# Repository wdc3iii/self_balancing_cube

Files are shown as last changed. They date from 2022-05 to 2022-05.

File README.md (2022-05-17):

# Table of Contents

* TOC
{:toc}

# Introduction
This project tackles a classic linear controls problem: balancing an inherently unstable system, and making the system robust to physical disturbances.  Taking inspiration from the rather impressive [Cubli](https://robohub.org/swiss-robots-cubli-a-cube-that-can-jump-up-balance-and-walk-across-your-desk/) robot, a 15cm cube capable of jumping up to balance on an edge or a corner, I set out to design a cube capable of stabilizing itself on an edge.  While the corner and jumping techniques of the Cubli are interesting, I would be more interested in continuing this project in an adaptive control direction, potentially making the cube robust to changes in center of mass (perhaps by adding weights to the corners during operation).  Over the course of a semester, mechanical, mechatronic, and control designs were implemented, and the resulting system was quite robust to external disturbances.  
# System Modeling
Because the cube is being balanced on an edge, it only needs to be modeled in two dimensions.  The FBD for the cube is shown:

The main forces to consider are the forces of gravity on the cube, the reaction forces at the ground, the torque applied by the motor, and the damping forces at the wheel and the cube. The equations of motion can be written:
$$\sum{M_c^o}=(m_w + m_c)l_csin(\theta_c)+T+C(\dot\theta_w - \dot\theta_c)=I_c^o\ddot\theta_c$$ $$\sum{M_w}=T-C(\dot\theta_c - \dot\theta_w)=I_w\ddot\theta_w$$
The inertia properties were approximated from theory by treating the cube as composed of one-dimensional rods, the wheel as a ring, and the battery as a rectangular prism.  Moments of inertia were transformed to the relevant axis by the parallel axis theorem.  
To simplify the controller design, the damping characteristics of the system were considered to be negligible.  This decouples the two governing equations, which are no longer dependent upon one another.  A single equation now needs to be controlled:
$$I_c^o\ddot\theta_c=(m_w + m_c)l_csin(\theta_c)+T$$
Linearizing this equation about the operating point $(\theta_c=0)$ using $sin(\theta)\approx \theta$ gives:
$$I_c^o\ddot\theta_c=(m_w + m_c)l_c\theta_c+T$$
For controller design, this is expressed in state space as:
$$
  \begin{bmatrix}
   \dot\theta_c \\
   \ddot\theta_c
  \end{bmatrix} = 
  \begin{bmatrix}
    0 & 1 \\ a & 0
  \end{bmatrix}\begin{bmatrix}
    \theta_c \\ \dot\theta_c
  \end{bmatrix} + \begin{bmatrix}
    0 \\ b
  \end{bmatrix} T
$$
Where $a = \frac{(m_w + m_c) l_c}{I_c^o}$ and $b = \frac{1}{I_c^o}$.

# System Design
The mechanical system is designed in SolidWorks, and is composed of two primary 3D printed parts, the frame and wheel.  The wheel is manufactured to have an adjustable mass, where bolts and nuts are added around the circumference in a symmetric fashion to increase or decrease the wheel inertia.  Larger inertia of the wheel allows a higher torque to generate less acceleration of the wheel, increasing the time over which torque can be applied before hitting saturation limits on the motor; however, this also increases the magnitude of the gravitation torque destabilizing the system.  The system mass was chosen somewhat arbitrarily and worked well.  CAD files are included in the project's GitHub repo.  
CAD Design
The mechatronic design for this system was similarly straightforward and simple.  An IMU is used to determine orientation, which is placed near the pivot point to minimize the impact of linear accelerations on the complementary filter which is used to estimate orientation.  An ODrive motor controller, motor, and motor encoder are used to apply torque to the system, and a Teensy microcontroller runs the control system.  The system is powered by a LiPo battery, which is placed near the pivot point to minimize it's destabilizing torque.  A complete parts list is given below:

* [Teensy 4.1](https://www.pjrc.com/store/teensy41.html) Microcontroller [(Amazon)](https://www.amazon.com/PJRC-Cortex-M7-Processor-iMXRT1062-Without/dp/B088JY7P2H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)
* ODrive v3.6 Motor Controller [(ODrive Shop)](https://odriverobotics.com/shop/odrive-v36)
* D5065 270kv Dual Shaft Motor [(ODrive Shop)](https://odriverobotics.com/shop/odrive-custom-motor-d5065)
* 20480 CPR Encoder [(ODrive Shop)](https://odriverobotics.com/shop/20480-cpr-encoder-with-odrive-cable)
* ICM 20480 IMU [(Sparkfun)](https://www.sparkfun.com/products/15335)
* 3300mAh 14.8V (4S) 100C LiPo Battery [(Amazon)](https://www.amazon.com/3300mAh-Graphene-Connector-Airplane-Quadcopter/dp/B082TRLPWQ?th=1)

Mechatronic Design
Mechatronic Design
# System Control

## State Observation
To design a state space controller, the entire state information must be accessible. To do this, partial observer is designed, the complementary filter, to combine acceleration and angular velocity measurements from the IMU into an estimate of the cube’s orientation. Two methods exist to estimate orientation from the IMU: integration of angular velocity, and the geometry of the gravity vector, shown in the equations below.  Both equations reference the quantities shown in the figure below.
Complementary Filter IMU Measurements
$$\theta^i_{c,gyro}=\theta^{i-1}_c + \omega_y \Delta t$$
$$\theta^i_{c,accel}=tan^{-1}{\frac{a_x}{a_z}}$$
Because gyroscope measurements are prone to drift, the gyroscope method is accurate in the short term, and tracks high frequency movements well; however, its long-term accuracy and low-frequency characteristics are poor. Conversely, the acceleration method tracks low-frequency movements well, and 
has good long-term accuracy. The complementary filter combines both estimates in an infinite-impulse response filter, given below:
$$\theta^i_c=\alpha \theta^i_{c,gyro} + (1 - \alpha)\theta^i_{c,accel}\quad 0 \ll \alpha < 1$$
With this computation, the entire system state is estimated, as $\dot\theta_c=\omega_y$ is observed directly.
## Controller Design: Pole Placement via State Space
Before designing the state space controller, controllability must be checked:
$$C_m = \begin{bmatrix}B & AB\end{bmatrix} = \begin{bmatrix}0 & b \\ b & 0\end{bmatrix} \rightarrow Full Rank, Controllable$$
Time specifications are given by desired system characteristics, at settling time of $t_s = 1$ and a maximum overshoot of $M_p = 0.05 = 5%$:
$$M_p = 0.05 \rightarrow \zeta = \frac{-ln(M_p)}{\sqrt{\pi^2 + ln^2(M_p)}}=0.69$$
$$t_s = 1\rightarrow\omega_n=\frac{4}{t_s\zeta}=5.79$$
These metrics determine the system's closed loop characteristic equation:
$$s^2 + 2\omega_n\zeta s + \omega_n^2=s^2+8s + 33.5960$$
The poles of the closed loop system can be placed accordingly:
$$det(sI - (A-BK))=|\begin{bmatrix}s & -1 \\ -a + k_1 b & s + k_2 b\end{bmatrix}|=0$$
$$s^2 + k_2 b s + a - k_1 b = s^2 + 8s + 33.5960$$
$$k_1 = 2.29\quad k_2 = 0.201$$
A few details of the controller implementation deserve notes. First, due to wires, and asymmetry, the center of mass of the device is slightly misaligned with the z-axis of the IMU, as shown in the figure below.
CoM Misalignment
To correct for this, the device is balanced by hand, and this offset angle is measured. The offset can then be subtracted so that the device balances over its center of mass instead of the IMU Z axis. Secondly, the control loop is implemented at a rate of 200Hz. It is assumed that this is a sufficiently fast update rate to ignore the discrete control aspects of the controller and treat it as continuous.
# Performance
Performance is perhaps most enjoyably evaluated by simply watching videos:
## TODO: Add performance videos

For more quantitative metric, consider the steady state operation, which maintains a deviation of less than $0.3\degree$. 
Steady State Performance
When rejecting a sizable disturbance, the following response was generated, with a settling time of 1.6s:
Disturbance Rejection
Overall, the cube is quite stable.  

The main performance limitation is the fact that the speed of the cube's wheel is not being controlled.  Because of this, repeated perturbations in one direction will repeatedly accelerate the wheel in the same direction.  After only a few such perturbations, the speed of the motor will saturate, and the motor will no longer be able to deliver torque to correct for further disturbance.  This is easily corrected by regulating the wheel speed to zero as well; however, in order for this system to be controllable, the damping between the frame and wheel must be accurately characterized.  An initial look at this damping shows it to be quite nonlinear, which will make this problem much more difficult. 
 
# Conclusion
The results of this project were quite strong.  The project was a very straightforward application of linear control techniques, and balancing was achieved quickly and with no parameter tuning.  In the future, I would like to target regulating the wheel velocity to zero, and potentially look into adaptive control methods which estimate the position of the center of mass in real time, and can adapt to changes, such as adding masses to one side of the cube.

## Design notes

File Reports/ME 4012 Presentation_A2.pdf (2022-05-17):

Will Compton, Domenic DiCarlo, Thalmus McDowell, Micah Morris – Group A2
ME 4012 Modeling and Control of Motion Systems

Spring 2022 Final Project Presentation

# Cue-B Final Project Presentation

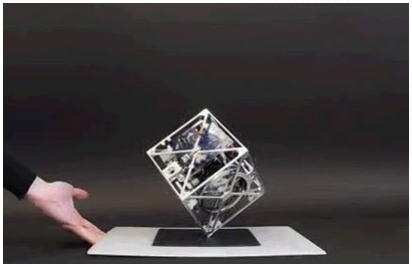
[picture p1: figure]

- Reaction-wheel controlled self-balancing cube
- Inspiration taken from Cubli
- Cube that can balance, stand, and "walk"
- System is not naturally stable (gravity)
- Control needed for balance

## Motivation

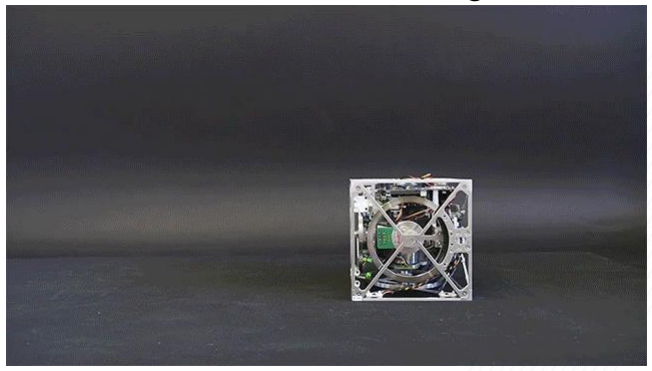
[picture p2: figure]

Cubli – Standing up

Cubli - Balancing

## Design

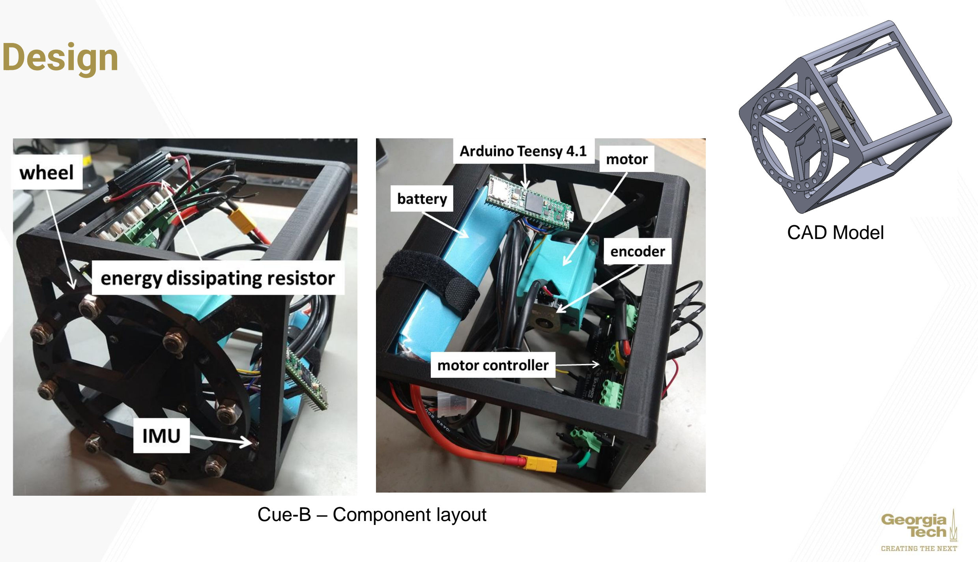
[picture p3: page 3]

CAD Model

Cue-B – Component layout

- IMU senses changes in angular acceleration/velocity
- IMU positioned on pivot point
- Battery is placed above pivot point to make control easier by lowering center of mass
- Reaction wheel has mass distributed far from center: maximize inertia, minimize mass
- Motor drives reaction wheel to produce torque to achieve stability
- ODrive motor controller has a torque mode where torque can be commanded directly

## Design

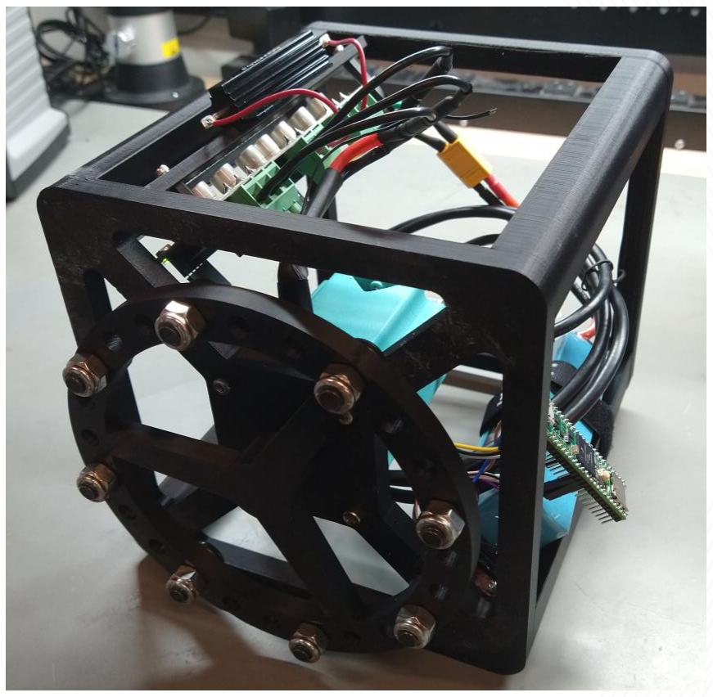
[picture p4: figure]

Cue-B – Assembled

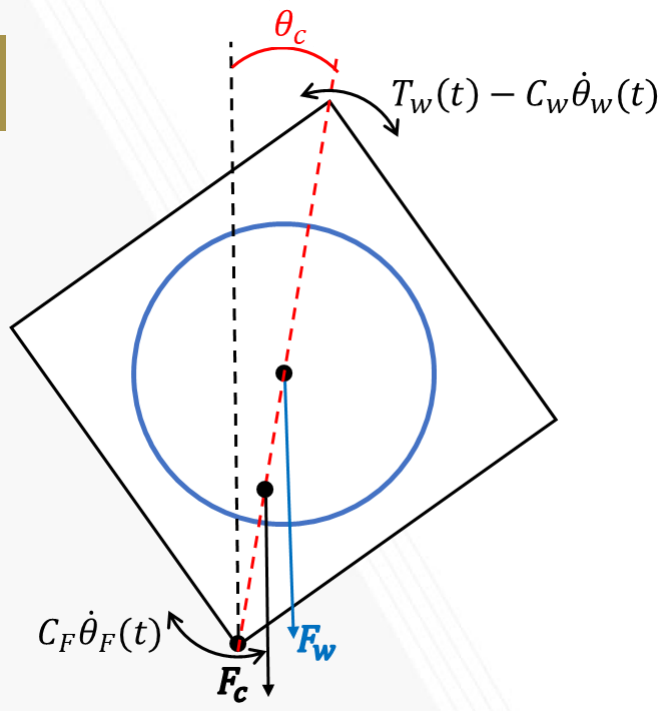
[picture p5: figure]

## Model

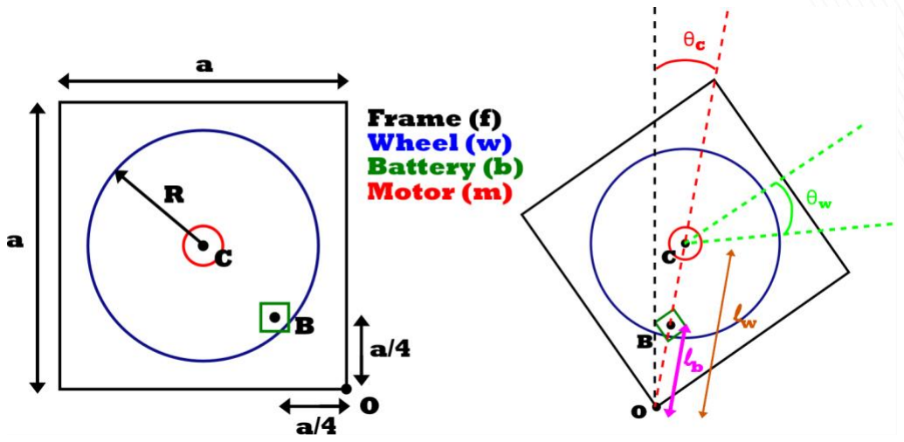
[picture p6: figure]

State Equations

θሶ
c
θሷ
c

=

0 | 1
1

Ioc

mwlw + mc

| lc g 0

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
Y = 1 0 θc θሶ c

θሶ
c
θሷ
c

=

0 1
a 0
| θc θሶ c +
| 0 b
Tw
Y = | 1 0 θc θሶ c
Variable | Meaning
θc | Angular displacement of COM
θሶw | Angular velocity of wheel
mw | Mass of the Wheel
mc | Mass of everything excluding wheel (applied at COM)
Tw | Torque applied by motor
lw | Distance from pivot to wheel (center of frame)
lc | Distance from pivot to COM

## Modeling Assumptions

- Negligible mechanical damping (motor, joint with ground, air resistance)
- Justification: these sources of damping are small, and typically aid stability rather than degrade it
- Reason: decouples the interaction of the wheel and the frame (damping would couple through velocity related effects)
- This allows the system to be approximated as second order, greatly simplifying analysis and controller design.

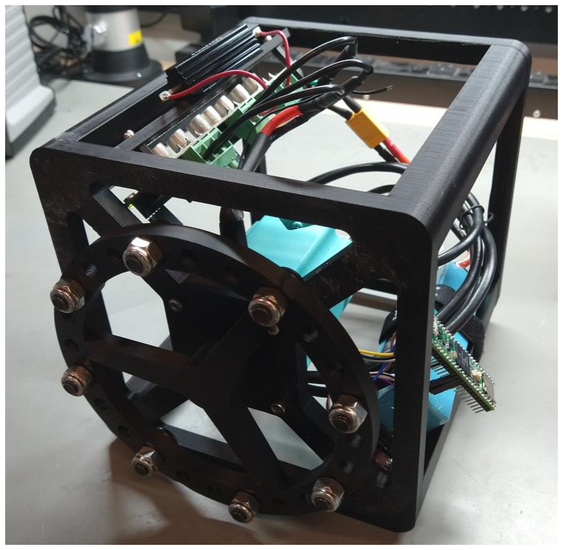
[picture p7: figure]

## Modeling Assumptions

- The ODrive torque controller is fast enough that it’s dynamics are negligible.
- Justification: The ODrive is a highly capable BLDC motor controller, paired with a 20480 CPR encoder, should enable precise and fast torque control
- Reason: Allows model to treat torque commands as taking place instantaneously, without having to model the dynamics of the motor controller.

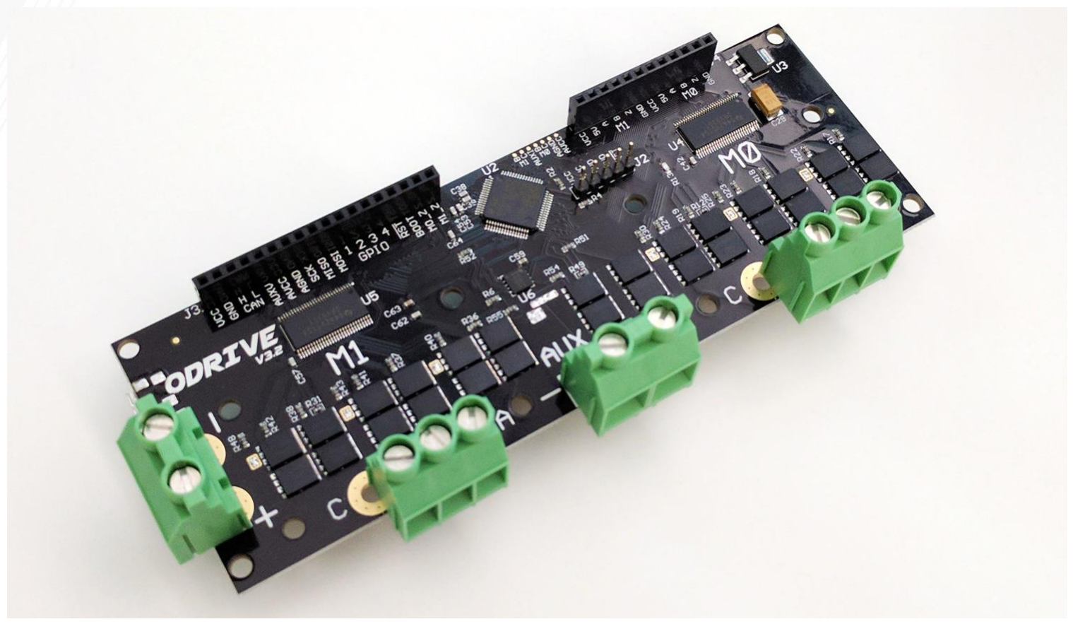
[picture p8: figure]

- The angle of the center of mass of the cube, θc
, cannot be measured
directly
- An Infinite Impulse Response observer, the complementary filter, is used to estimate θc

## Controller Design: State Estimation

Geometry of Gravitational Acceleration | Integration of Gyroscope

θc,gyro

i | = θc

i−1 + ω∆t

zIMU

xIMU

g

ωy

θc

θc,accel

i = tan⁻¹

ax
az

Tracks low-frequency movements well No Drift
Inaccurate with high frequency

Tracks high-frequency movements well Prone to drift - inaccurate with low frequency

θc

i = αθc,gyro

i | + 1 − α θc,accel i

0 ≪ α < 1

- System model is approximated as linear second order
- State space control selected to place poles
- Controllability
- Time Specifications:
- Settling time, ts = 1s
- Maximum Overshoot, Mp = 0.05 (5%)

## Controller Design: State Space

Mp = 0.05 → ζ =

ln Mp

π

2 + ln² Mp

= 0.69 | ts = 1 → ωn =

4
tsζ

= 5.79

CLCE: s

2 + 2ζωns + wn

2 = s

2 + 8s + 33.5960 = 0

CM = | B AB | =

0 b
b 0

→ Full Rank, Controllable

- Closed Loop Characteristic of State Space System

## Controller Design: State Space

CLCE: det sI − A − BK = 0

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
k1 | k2 | = 0
s | −1
−a + k1b s + k2b | = 0

s

2 + k2bs + a − k1b = s

2 + 8s + 35.596 = 0

k1 = 2.29 k2 = 0.201

- Teensy 4.1 is a fast and capable microcontroller
- Communication with IMU is performed over SPI at 7MHz
- Both complementary filter and control loop are implemented in the same callback function
- This callback is tied to a hardware timer at 200Hz
- This speed is sufficiently fast to ignore the difference between the discrete and continuous implementations of the controller.

## Results: Implementation

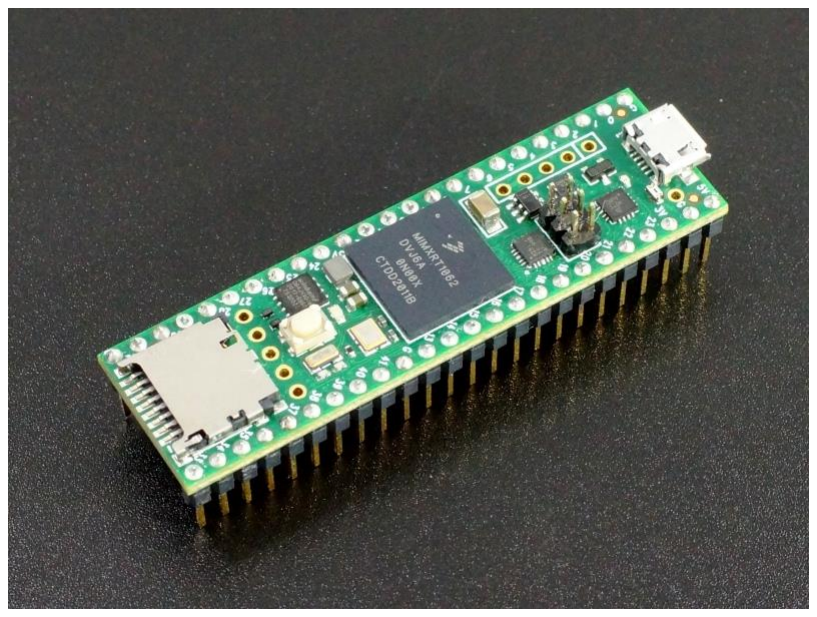
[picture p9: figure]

## Results: Implementation

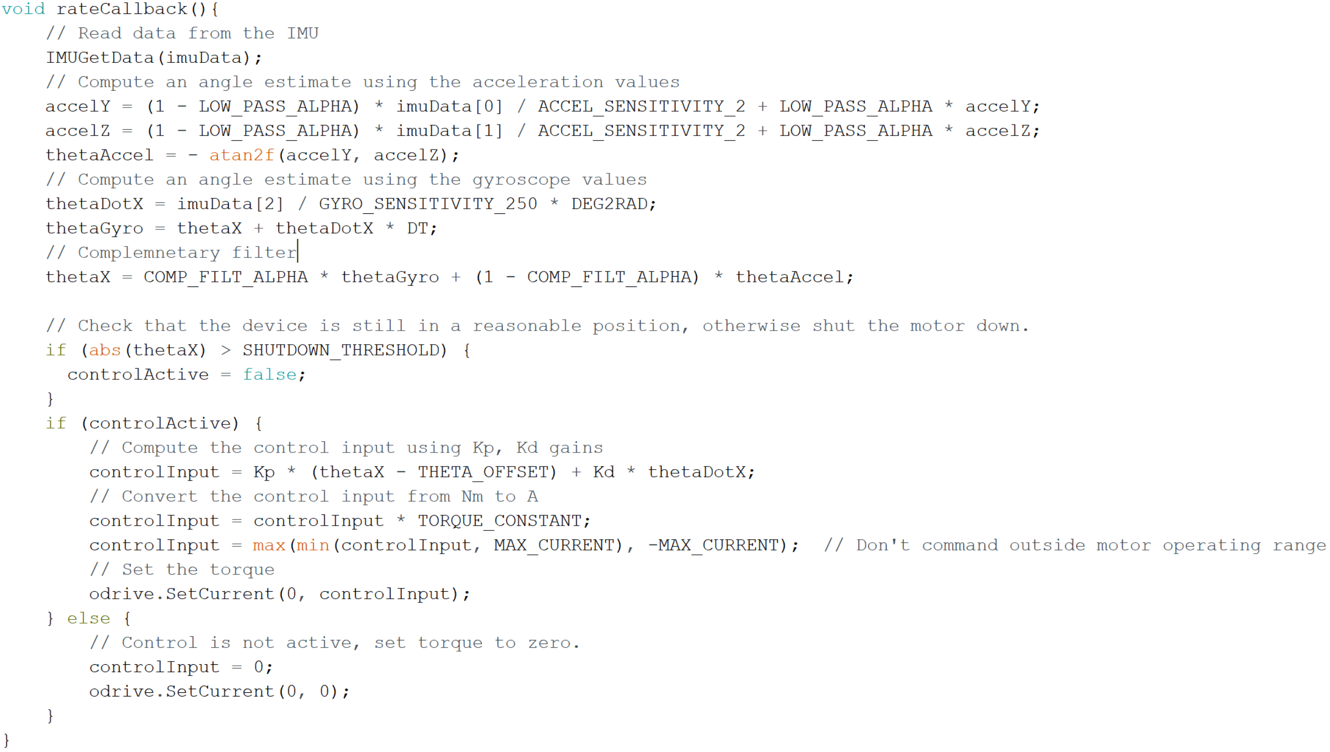
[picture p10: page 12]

- Teensy 4.1 is a fast and capable microcontroller
- Communication with IMU is performed over SPI at 7MHz
- Both complementary filter and control loop are implemented in the same callback function
- This callback is tied to a hardware timer at 200Hz
- This speed is sufficiently fast to ignore the difference between the discrete and continuous implementations of the controller.

## Results: Implementation

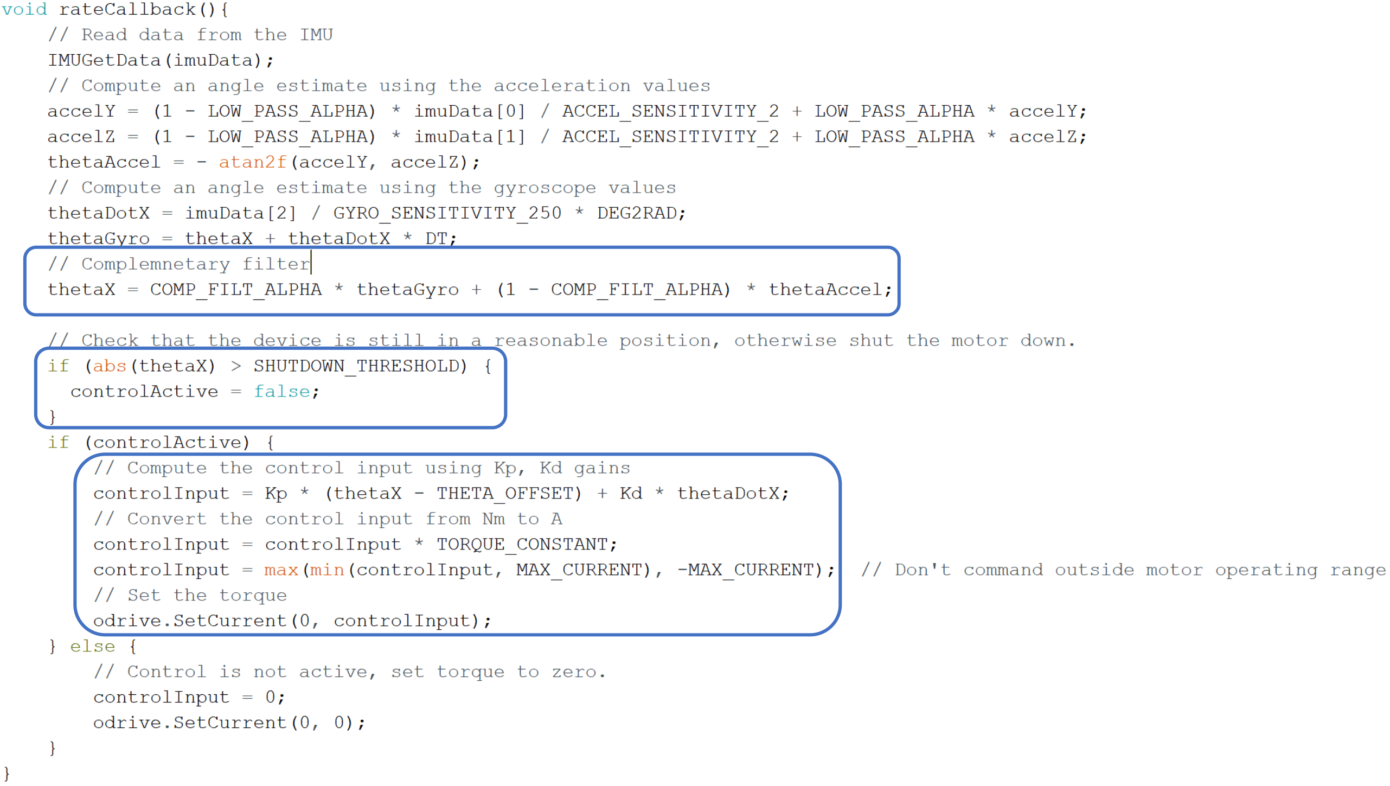
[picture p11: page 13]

- Teensy 4.1 is a fast and capable microcontroller
- Communication with IMU is performed over SPI at 7MHz
- Both complementary filter and control loop are implemented in the same callback function
- This callback is tied to a hardware timer at 200Hz
- This speed is sufficiently fast to ignore the difference between the discrete and continuous implementations of the controller.

## Results: Implementation

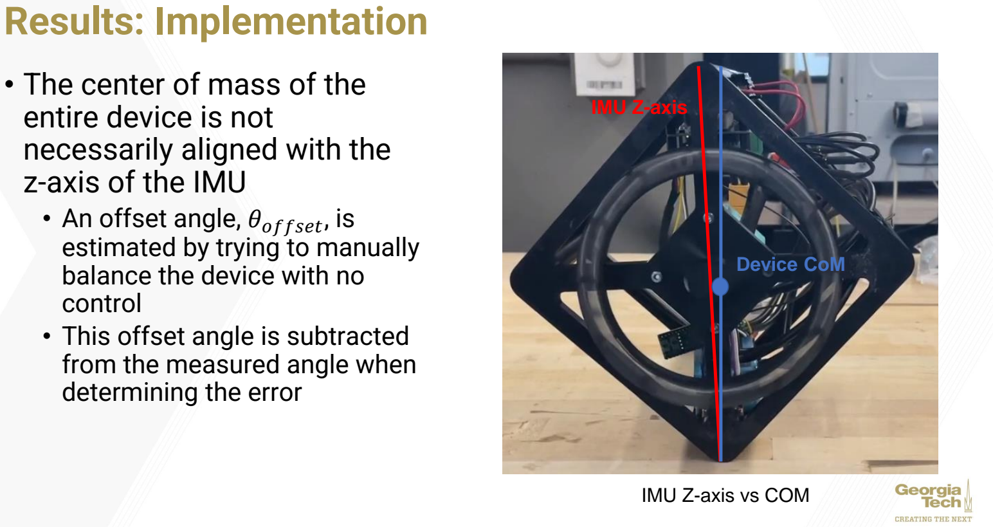
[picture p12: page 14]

- The center of mass of the entire device is not
necessarily aligned with the z-axis of the IMU
- An offset angle, θoffset, is estimated by trying to manually balance the device with no control
- This offset angle is subtracted from the measured angle when determining the error

IMU Z-axis

Device CoM

IMU Z-axis vs COM

## Results: Simulation

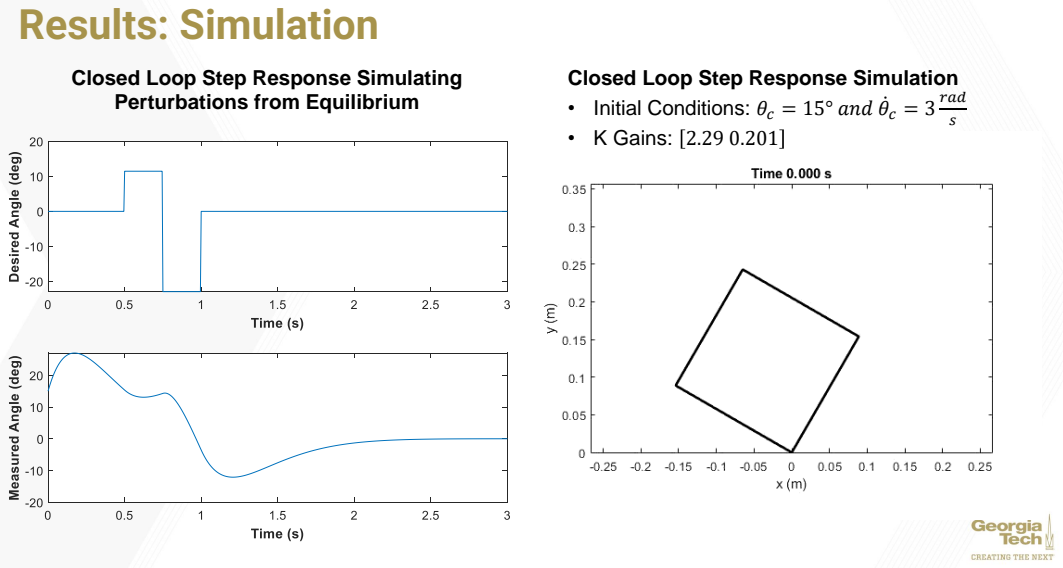
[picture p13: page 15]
rad; • K Gains:

Closed Loop Step Response Simulating
Perturbations from Equilibrium

Closed Loop Step Response Simulation
• Initial Conditions: θc = 15° and θሶ

## Results: Steady State Balancing on Device

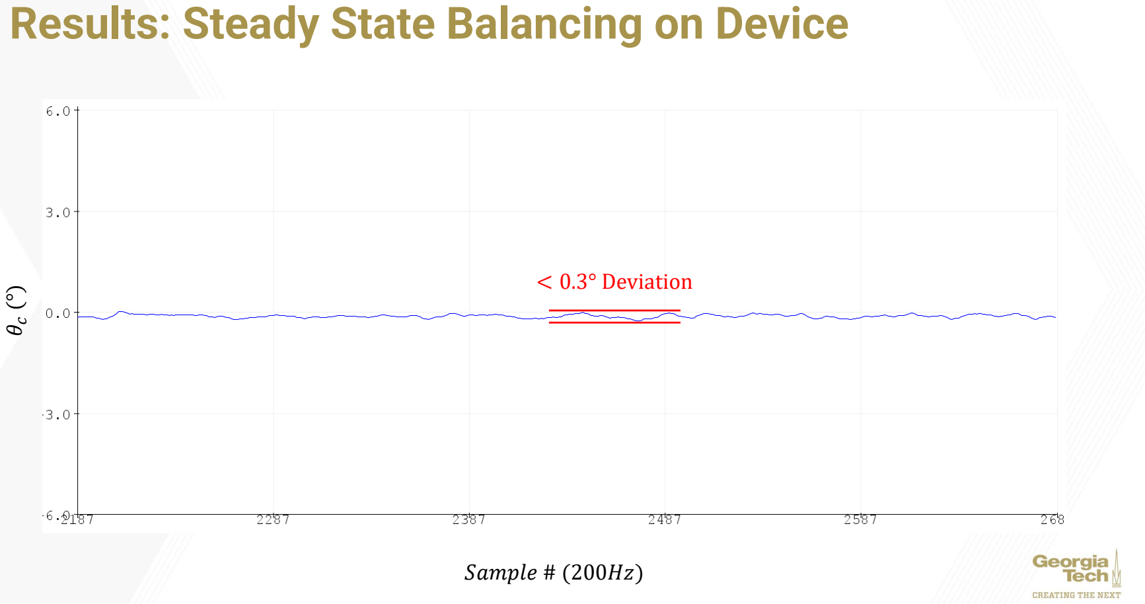
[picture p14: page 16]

θ

c

(

°

)

Sample # (200Hz)

< 0.3° Deviation

## Results: Disturbance Rejection on Device

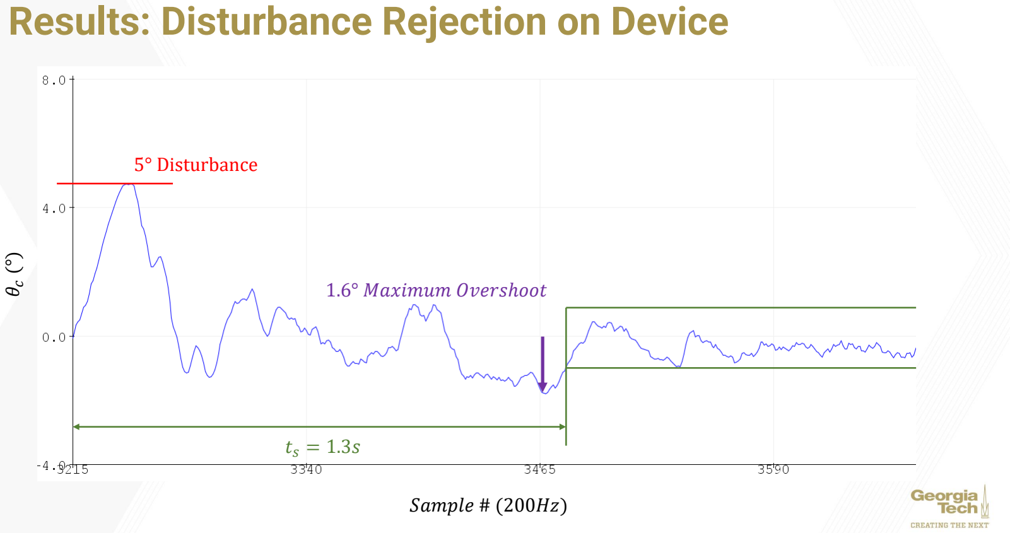
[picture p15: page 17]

θ

c

(

°

)

Sample # (200Hz)

5° Disturbance

ts = 1.3s

1.6° Maximum Oversℎoot

## Video

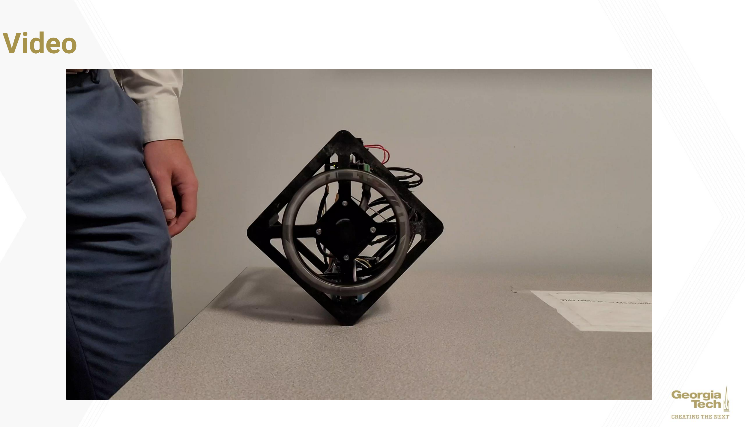
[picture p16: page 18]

Cue-B Controlled With State Space K Gains

## Conclusion

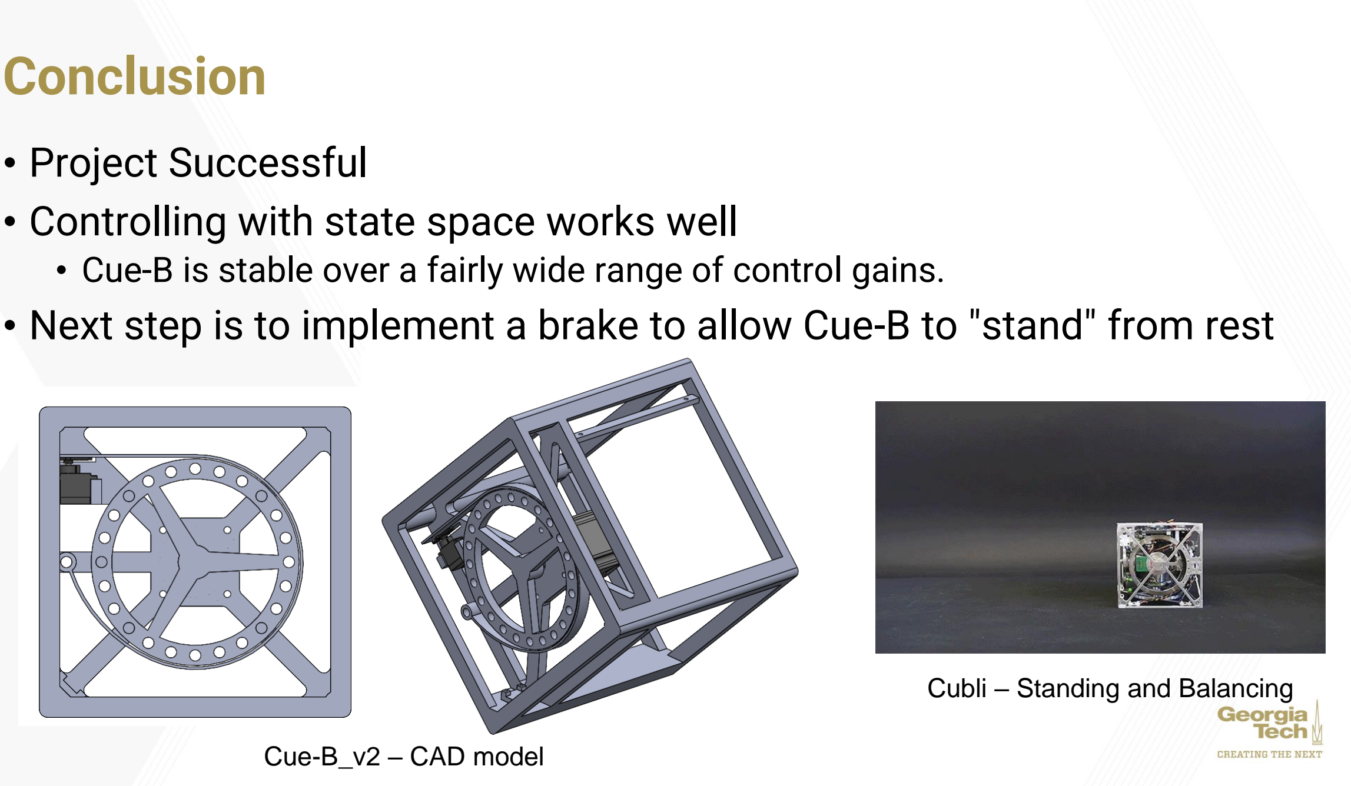
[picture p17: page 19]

- Project Successful
- Controlling with state space works well
- Cue-B is stable over a fairly wide range of control gains.
- Next step is to implement a brake to allow Cue-B to "stand" from rest

Cue-B_v2 – CAD model

Cubli – Standing and Balancing

## Questions?

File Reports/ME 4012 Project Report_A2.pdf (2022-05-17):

## ME 4012 Project Report: Cue-B

Will Compton, Domenic DiCarlo, Thalmus McDowell, and Micah Morris
ME 4012 Modeling and Control of Motion Systems

Abstract
Taking inspiration from the project Cubli [1], Team A2 sought to design and construct a cube capable of balancing on an edge using a reaction wheel. Balance through the wheel was achieved using state space and pole placement via Ackerman’s method. The control system was implemented through an Arduino Teensy and ODrive motor and motor controller. Ultimately, balance was achieved along with adequate disturbance rejection. Future improvements could include a control scheme to make the cube stand up onto an edge from an adjacent face, saturation avoidance through the inclusion of wheel velocity as a state, and potentially additional reaction wheels to achieve vertex balance alongside edge balance.

Introduction
Team A2 has decided to develop a reaction wheel-controlled cube that launches from rest to balancing on an edge. Balancing items is inherently unstable, as slight adjustments to position can cause tipping and falling; therefore, to balance without external input, control mechanisms will need to be put into place. This project was inspired by demonstrations of the research project Cubli, a small self-balancing cube that is capable of not only balancing on edges but also balancing on vertices as well as “walking” by rolling itself from face to edge to adjacent face. The dexterity of Cubli was impressive, and the team sought to emulate it in more conservative respects.

Design
The components of Cue-B that were purchased are the motor and motor controller. The Arduino Teensy 4.1, IMU, Encoder, battery, and ball bearings were all components that the group already owned. The parts that were manufactured include the wheel, the frame of Cue-B, and the motor mount. The main components of Cue-B are the reaction wheel, motor, and IMU. The torque from the reaction wheel is used to balance and control Cue-B. The shape of the reaction wheel was optimized to maximize the moment of inertia with the minimal amount of mass possible. Bolts were distributed along the outer ring of the wheel to increase its inertia. The motor drives the reaction wheel to stabilize Cue-B. It is controlled by an O-drive. The O-drive is great because it has a torque mode that allows direct control of the motor’s torque. The IMU determines the orientation of the cube so that the reaction wheel can respond accordingly. The IMU was placed on the pivot point of Cue-B to get the most accurate readings. Another important design choice is the location of the battery; it was placed on the pivot point as well. The battery’s location makes it easier for Cue-B to be controlled because it lowers the center of mass. Therefore, less torque will be needed to correct Cue-B when it falls from the equilibrium position. The setup of Cue-B can be found in Figure 1.

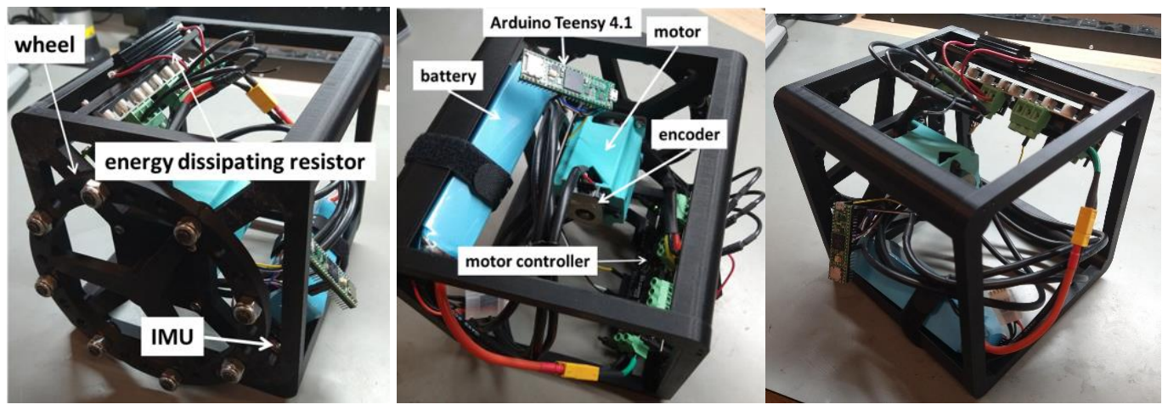
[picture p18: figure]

Figure 1: Mechanical design and Electrical components of the Cue-B.

Modeling
Cue-B was modeled as a square with sharp corners. To determine the dynamic equations a free body diagram was created, illustrated in Figure 2:

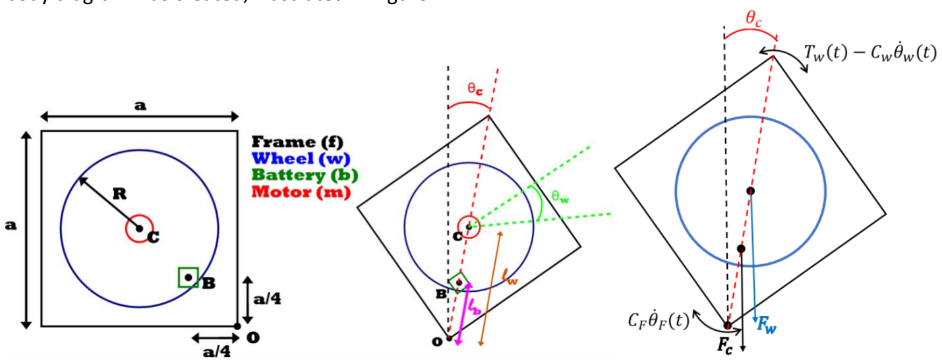
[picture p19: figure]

Figure 2: Cue-B parameters and free body diagram

As shown above, the free body diagram uses a square rotated θc
from the origin. This represents the instantaneous moment when the cube is rotated away from its balance point. This orientation was chosen because Cue-B is meant to be controlled about its balancing point, which is represented by θc = 0. Two moment balance equations were used to determine the dynamic equations. Equation 1 was created from a moment balance about point O. Equation 2 was created from the moment on the wheel. The dynamic equations for the system in Figure 2 are,

∑ Mc

o = Io

cθ̈
c

(t) = mwglw sin(θc

) + mcglc sin(θc

) − Tw(t) + Cwθ̇w(t) − Ccθ̇
c
(t) | (1)

Mw = Iw (θ̈
F
(t) + θ̈w(t)) = Tw(t) − Cwθ̇w(t) | (2)

[2] was referenced to create the dynamic equations of motion. The variable definitions can be found in Table 1:

Table 1: Variable definitions
Definition | Variable
Torque of the Wheel | Tw
Angle of Cube relative to the vertical | θc
Angle of wheel | θw
Mass of the frame | mF
Mass of the battery | mb
Mass of the motor | mm
Mass of the wheel | mw
Mass of the cube | mc = mF + mb + mm + mw
Length to center of wheel | lw
Length to the center of mass of the cube | lc
Radius of the wheel | Rw
Radius of the motor | Rm
Length of the cube | a
Coefficient of friction on wheel axle | Cw
Coefficient of friction on rotation point of Cue-B | Cc
Acceleration due to gravity | g
Moment of Inertia of the Cube | c = Io F + Io w + Io m + Io b Io
Moment of Inertia of the Wheel | Io w = mw (Rw 1 ) 2 + a 2 2
Moment of Inertia of the Battery | 7 Io b = 2 mba 24
Moment of Inertia of the Motor | mm Io m = (Rm 2 + a 2 ) 2
Moment of Inertia of the Frame | Io mF (4a a 2 ) F = 2 + 6 4

The length and radius measurements a, lw, Rw and Rm was found using SolidWorks and a ruler. The length to the center of mass of the cube, lc
, was determined algebraically using the center of mass equation. The masses mb and mm was determined from the battery and motor provided specifications. The mass of the wheel and the frame, mw and mF, were weighed using a scale. The moments of inertia for the components, Io

w, Io

b
, Io

m, Io

F
, were determined using the known equations of similar geometries and then translating them from their center of mass to the rotation point O. For example, Io

w was
estimated using the moment of inertia of a hollowed cylinder translated to the pivot point O. The value of the coefficients of friction, Cw and Cc

, was of the magnitude of 10⁻⁴ [2]. For simplification, the coefficients will be ignored when developing the state space representation.
The dynamic equations (1) and (2) involve a nonlinear term sin(θc

) thus, Equation 1 must be linearized. The equation was linearized about the balancing point θc0 = 0° because that is the angle that Cue-B was controlled about. The resulting equation is,

Io

cθ̈
c

(t) = mwglwθc + mcglcθc − Tw(t) + Cwθ̇w(t) − Ccθ̇
c
(t) | (3)

With the linearized moment equation of the cube, (3), and the moment of the wheel equation, (2), a Laplace transform was conducted to find the transfer function of the system. The Laplace transform was conducted in terms of θF(s), θ̇w(s), and Tw(s). The desired transfer function is of the form θF(s)
Tw(s)

. This
transfer function uses a torque input to control the desired angle of the cube. The motor used on Cue-B is torque controllable, which simplifies the transfer function because there is no need for a transfer function relating the angular velocity of the motor to the torque of the motor. The resulting transfer function is,
θF(s)
Tw(s)

= −

s
(CwIw+Cc

)s

2+(Io

c−mwglw−mcglc+CwCc
)s+CwIo

c−Cwmwglw−Cwmcglc

(4)

From the dynamic equations a state space representation was also derived. Cue-B was controlled using state space techniques which will be expounded upon in the Controller Design section. The state space equations, given in Equations 5 and 6, simplify the model of the system by neglecting mechanical damping in the system.

[

θ̇
c
θ̈
c

] = [

0 | 1
(

1

Ioc

) (mwlw + mc
lc
| )g 0

][
θc
θ̇
c

] + [
0
1

Ioc] Tw = [
0 1
a 0

][
θc
θ̇
c

] + [
0
b
]Tw | (5)

Y = [1 0][
θc
θ̇
c
] | (6)

Controller Design
To design a state space controller, the entire state information must be accessible. To do this, partial observer is designed, the complementary filter, to combine acceleration and angular velocity measurements from the IMU into an estimate of the cube’s orientation. Two methods exist to estimate orientation from the IMU: integration of angular velocity, shown in equation 7, and the geometry of the gravity vector, shown in equation 8, where both equations reference the quantities shown in Figure 3.

Figure 3: The quantities measured by the IMU. Z and X reference the axes along which accelerations will be measured, and ωy is the angular velocity about the remaining axis.

θc,gyro

i | = θc
i−1 + ω∆t | (7)

θc,accel

i = tan⁻¹ ax
az

(8)

Because gyroscope measurements are prone to drift, the gyroscope method is accurate in the short term, and tracks high frequency movements well; however, its long-term accuracy and low-frequency characteristics are poor. Conversely, the acceleration method tracks low-frequency movements well, and has good long-term accuracy. The complementary filter, equation 9, combines both estimates in an infinite-impulse response filter [3].

θc

i = αθc,gyro

i | + (1 − α)θc,accel

i
, 0 ≪ α < 1 | (9)

With the state estimated (as θc

̇ = ωy), the controller can be designed via pole placement. First, controllability must be checked: CM = [B AB] = [

0 b
b 0

] → Full Rank, Controllable

Time specifications are given by desired system characteristics, at settling time of ts = 1 and a maximum overshoot of Mp = 0.05 = 5%:

Mp = 0.05 → ζ =

ln(Mp)
√π
2 + ln² Mp

= 0.69

ts = 1 → ωn =

4
tsζ

= 5.79

Which gives rise to the following desired closed loop characteristic equation: s

2 + 2ζωns + ωn

2 = s

2 + 8s + 33.5960 = 0
The poles of the closed loop system can then be placed accordingly. det(sI − (A − BK)) = |[

s 0
0 s

] − ([

0 1
a 0

] − [

0
b

][k1 k2])| = 0
s | −1
−a + k1b s + k2b

| = s
2 + k2bs + a − k1b = 0

s

2 + k2bs + a − k1b = s

2 + 8s + 35.596 = 0
k1 = 2.29 k2 = 0.201
A few details of the controller implementation deserve notes. First, due to wires, and asymmetry, the center of mass of the device is slightly misaligned with the z-axis of the IMU. To correct for this, the device is balanced by hand, and this offset angle is measured. The offset can then be subtracted so that the device balances over its center of mass instead of the IMU Z axis. Secondly, the control loop is implemented at a rate of 200Hz. It is assumed that this is a sufficiently fast update rate to ignore the discrete control aspects of the controller and treat it as continuous.

Experimental Results (and Simulation Results)
The closed loop system is first simulated to ensure that the designed response characteristics are correct. The results of the simulation are shown in Figure 4.

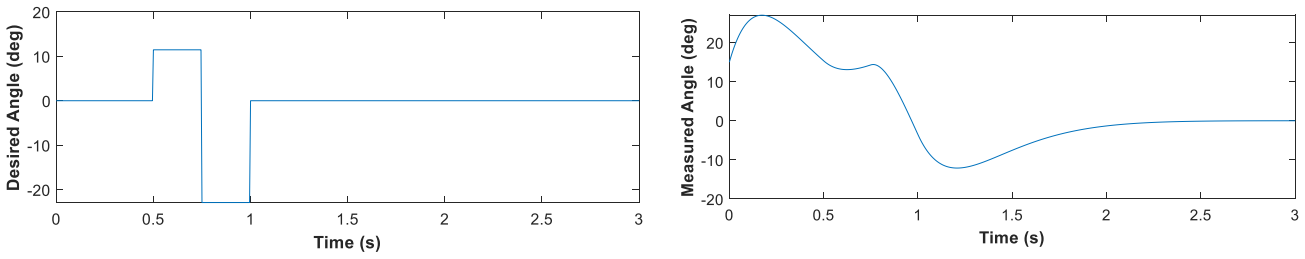
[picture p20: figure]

Figure 4: The input desired angle (left) and resulting system response (right). The simulated response confirms closed loop design characteristics.

The closed loop system performed exceptionally well. Shown in Figure 5, the steady state behavior of the device-maintained balance within 0.3° of the desired vertical position. The device has significant disturbance rejection capability and could withstand significant pushes or pulls on the frame. Figure 5 shows a 5° disturbance, which settles to within a degree after 1.3 seconds, and has a maximum overshoot of 1.6°. These response characteristics do not quite meet the design specifications; this is likely due to the several modeling assumptions which were made in the design of the controller (negligible damping, negligible motor dynamics due to ODrive torque controller, negligible effects of discrete microcontroller control). However, the device is exceptionally stable, which was the original design intent, so the design specifications have successfully served their purpose in the design of a stable system.

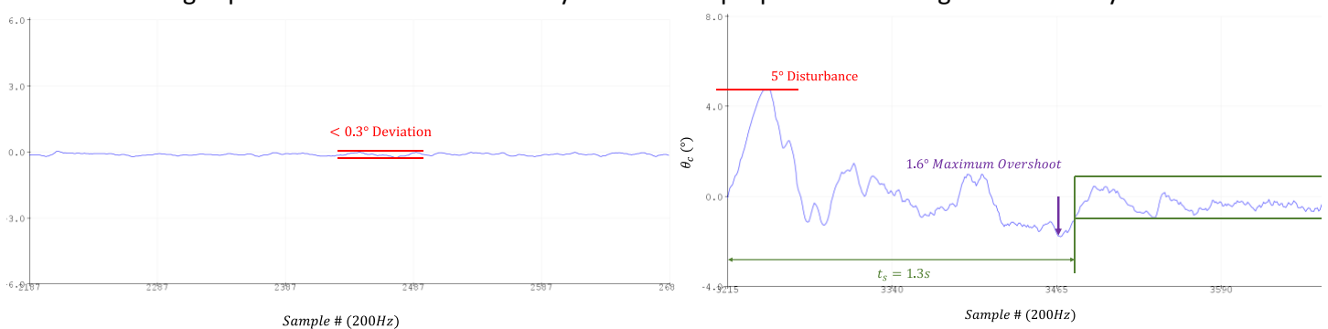
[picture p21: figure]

Figure 5: The controlled response of the cube, in steady state (left) and when rejecting a disturbance (right).
One note on performance is that because the wheel velocity is not included as a state, the reaction wheel’s speed will increase to saturation if the system is perturbed in one direction several times. This could be improved by including the reaction wheel speed in the model and driving this to zero. However, if damping is assumed to be negligible, the resulting state space system has the form:
[

θ̇
c
θ̈
c
ω̇w

] = [
0 1 0
a 0 0
0 0 0

] [
θc
θ̇
c
ωw

] + [
0
b
−c

] T

This system is in fact not controllable, indicating that the coupling between the wheel and the device due to damping is necessary to model (and model accurately) to control both the wheel speed and the cube angle. If damping is considered, the system is controllable. However, an analysis of the system damping showed it to be quite nonlinear: by running the motor up to some speed, and letting it coast to a stop, linear damping would generate an exponential decay time response. The observed response is very linear in time, indicating a constant damping force, rather than one which is proportional to speed. This function is not linear (it is discontinuous about the origin) and thus is somewhat difficult to model in a linear system. Future work could linearize the system about each side of the origin, characterize the damping fully in these regions, and use this damping model to control the reaction wheel speed.

Conclusion
Over the course of this project, the team constructed a reaction-wheel controlled cube capable of balancing on a single edge. State space control was implemented effectively, and consistent results were achieved. Improvements can be made to the system; a persistent issue was the motor reaching saturation after being disturbed in the same direction multiple times, as discussed in the Results section. Future work would follow as described above. Furthermore, an original goal of the project, standing up from a side using a braking system, was not achieved. If time allowed, implementation of this addition would add value to the project.

Acknowledgements
The team would like to thank Professor Mazumdar for her guidance with this project, as well as the Flowers Invention Studio for providing resources and equipment.

References
[1] M. Gajan and M. Waibel, “Cubli – a cube that can jump up, balance, and walk across your desk,” Robohub, 20-Dec-2013. [Online]. Available: https://robohub.org/swiss-robots-cubli-a-cube-that-can-jump-up-balance-and-walk-across-your-desk/. [Accessed: 22-Apr-2022].
[2] Liao T-L, Chen S-J, Chiu C-C, Yan J-J. “Nonlinear Dynamics and Control of a Cube Robot.” Mathematics. 8(10):1840, 2020 https://doi.org/10.3390/math8101840
[3] P.-J. Van de Maele, “Reading a IMU without Kalman: The complementary filter,” Creativity in Automation. [Online]. Available: https://www.pieter-jan.com/node/11. [Accessed: 18-Apr-2022].

ME4012 Grading Rubric for Final Project Report
Team/Project Name: Cue-B
Team Members: Will Compton, Domenic DiCarlo, Thalmus McDowell, Micah Morris
Metrics | Pts | Comments
Design or Simulation Assumptions (5 pts) *Is the design of the system well-described in the text? *What is the quality of the design, is it well thought out and executed well?

Model (30 pts) *Is the model section well-written and easy to follow? Is the model error-free? *Does the model accurately capture the relevant dynamics? *Are the equations of motion correctly derived? *Does the team do a good job of estimating the parameters of their plant? *Is there a table of derived/estimated parameters?

Controller Design/Implementation (30 pts) *Is the controller section well-written and easy to follow? *Does the controller design make sense? *Are they able to meet their desired design metric, achieve disturbance rejection, or achieve stability (for unstable systems)? *Does the team do a good job of implementing a working controller (Labview, Arduino, or Matlab)? *If the controller does not work, can they describe why and what they would change?

Experimental or Simulation Results (15 pts) *Are the results easy to follow and logically written? *Does the performance of the system match expectations from theory (compare nonlinear simulation with linear model, or compare model with experiment)? If not, did the team explain why? *Are there graphs/figures to show performance?

Final Paper Quality (20 pts) *Is the abstract/introduction/conclusion well written? *Are the figures captioned and readable? *Did the team make the figures/formatting look nice? *Are there references and are they correctly cited? *Is the paper error-free in terms of spelling and grammar? *Is the paper easy to read and easy to follow logically? *Did the team pick an appropriate level of difficulty for their team size? Where they able to implement what they set out to do? *Did the team finish construction and have a mostly working system? *Does the system work well enough for control?

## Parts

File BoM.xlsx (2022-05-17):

Self Balancing Cube Bill of Materials
Part | Purchase Location | Quantity | Unit Cost
Teensy 4.1 | https://www.amazon.com/PJRC-Cortex-M7-Processor-iMXRT1062-Without/dp/B088JY7P2H/ref=sr_1_4? | 1 | $31.35
ODrive v3.6 Motor Controller | https://odriverobotics.com/shop/odrive-v36 | 1 | $199.00
D5065 270kv Dual Shaft Motor | https://odriverobotics.com/shop/odrive-custom-motor-d5065 | 1 | $79.00
20480 CPR Encoder | https://odriverobotics.com/shop/20480-cpr-encoder-with-odrive-cable | 1 | $39.00
ICM 20480 IMU | https://www.sparkfun.com/products/15335 | 1 | $18.50
3300mAh 14.8V (4S) 100C LiPo Battery | https://www.amazon.com/3300mAh-Graphene-Connector-Airplane-Quadcopter/dp/B082TRLPWQ?th=1 | 1 | $114.99
 |  | Total: | $481.84

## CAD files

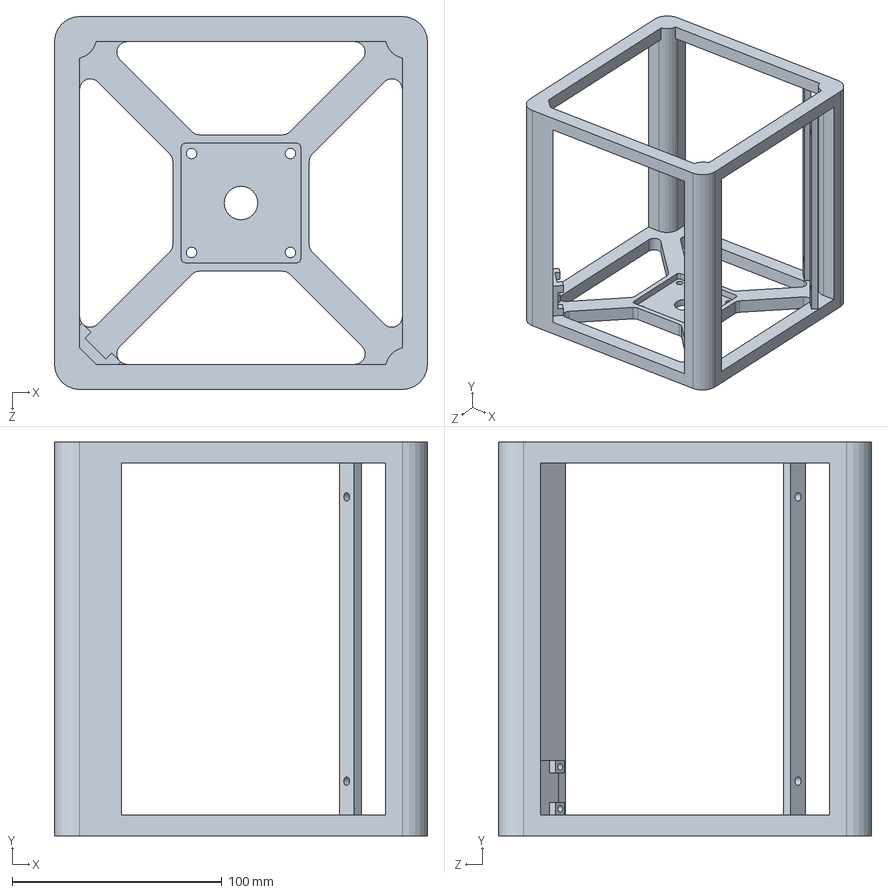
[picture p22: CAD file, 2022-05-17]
CAD/TestStandBody.SLDPRT
177.8 x 187.8 x 177.8 mm

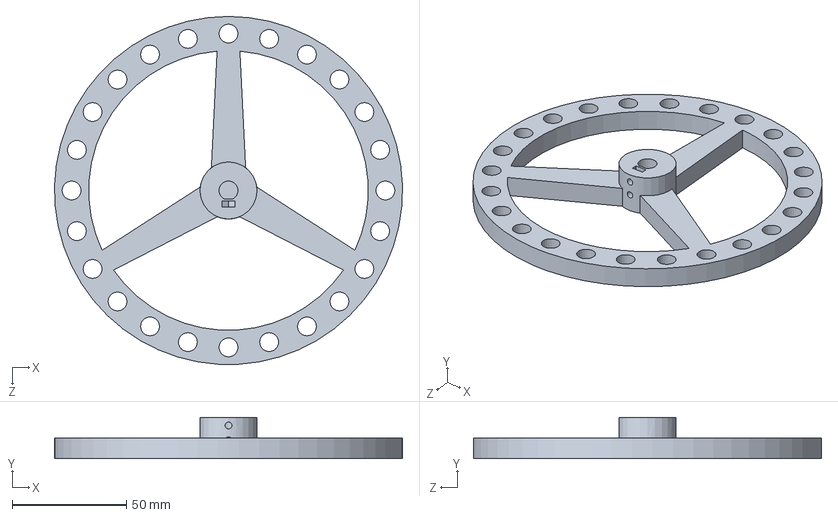
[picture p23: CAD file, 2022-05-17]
CAD/Wheel.SLDPRT
152.3 x 18.0 x 152.4 mm

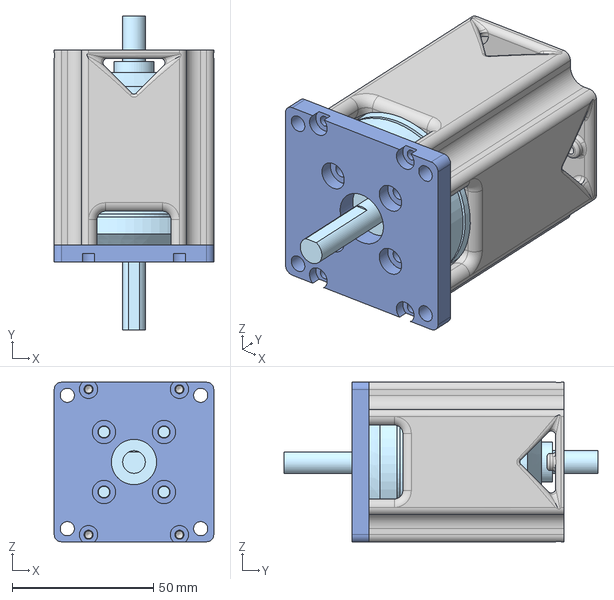
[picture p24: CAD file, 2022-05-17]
CAD/Enclosure_Natural_Cooling.step
56.4 x 111.0 x 56.4 mm

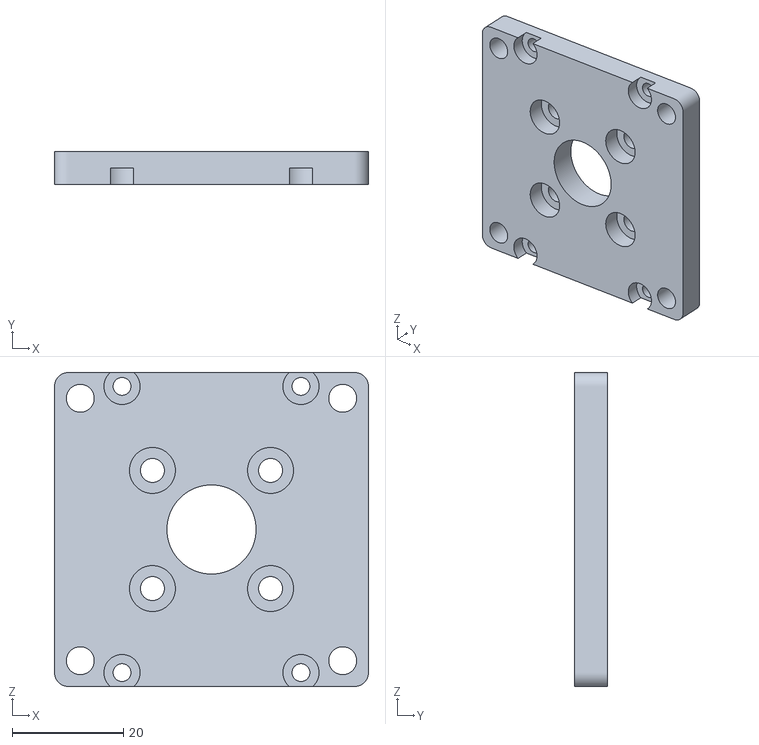
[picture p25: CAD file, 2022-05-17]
CAD/Enclosure_Plate.stl
56.4 x 6.00 x 56.4

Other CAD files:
CAD/TestStandBody.STL

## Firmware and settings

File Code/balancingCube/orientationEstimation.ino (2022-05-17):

#include "orientationHeader.h"
#include <SPI.h>


const uint8_t IMU_CHIP_SELECT = 10;
volatile float thetaY;
volatile int accelX;
volatile int accelZ;


void setup() {
    pinMode(IMU_CHIP_SELECT, OUTPUT);
    SPI.begin(); 
    
    // IMU Setup
    spi_IMU_write8(PWR_MNG, 0x80);  // Reset IMU
    delay(3000);
    spi_IMU_write8(PWR_MNG, 0x02);  // Select IMU clock
    spi_IMU_write8(USER_CTRL, 0xD0);
    // Set Gyro, Accel sensitivity, DLPF
    spi_IMU_setUserBank(USER_BANK_2);
    spi_IMU_write8(GYRO_CONFIG, GYRO_RANGE_250);
    spi_IMU_write8(ACCEL_CONFIG, ACCEL_RANGE_2);
    // Set power state
    uint8_t check1 = spi_IMU_read8(GYRO_CONFIG);
    uint8_t check2 = spi_IMU_read8(ACCEL_CONFIG);
    printf("%d", check1);
    printf("%d", check1);
    spi_IMU_setUserBank(USER_BANK_0);
}

void loop() {
    short data[3];
    float dt = 0.01;
    IMUGetData(&data);
    accelX = (1 - LOW_PASS_ALPHA) * data[0] + LOW_PASS_ALPHA * accelX;
    accelZ = (1 - LOW_PASS_ALPHA) * data[1] + LOW_PASS_ALPHA * accelZ;
    float thetaAccel = - atan2f((float) accelX, (float) accelZ) * 180 / M_PI;
    float gyroAccel = thetaY + data[2] * dt / GYRO_SENSITIVITY_250;
    thetaY = COMP_FILT_ALPHA * gyroAccel + (1 - COMP_FILT_ALPHA) * thetaAccel;
    Serial.println(thetaY);
}

void spi_IMU_setUserBank(uint8_t bank) {
    uint8_t reg = ~0x80 & 0xF7;
    digitalWrite(IMU_CHIP_SELECT, LOW);  // Set Slave select to low to begin transmission
    SPI.transfer(reg);                   // Tranfer the register
    SPI.transfer(bank);                  // Transfer the bank to select
    digitalWrite(IMU_CHIP_SELECT, HIGH); // Set slave select high
}

uint8_t spi_IMU_read8(uint8_t reg) {
    reg |= 0x80;                         // Set high bit on register to indicate read action
    digitalWrite(IMU_CHIP_SELECT, LOW);  // Set Slave select to low to begin transmission
    SPI.transfer(reg);                   // Transmit register to read from
    uint8_t RXData = SPI.transfer(0x00); // Send clock pulses, to receive data
    digitalWrite(IMU_CHIP_SELECT, HIGH); // Set slave select high
    return RXData;
}

short spi_IMU_read16(uint8_t regHigh, uint8_t regLow) {
    reg |= 0x80;                           // Set high bit on register to indicate read action
    digitalWrite(IMU_CHIP_SELECT, LOW);    // Set Slave select to low to begin transmission
    SPI.transfer(regHigh);                 // Transmit register to read from
    uint8_t highData = SPI.transfer(0x00); // Send clock pulses, to receive data
    SPI.transfer(regLow);                  // Transmit register to read from
    uint8_t lowData = SPI.transfer(0x00);  // Send clock pulses, to receive data
    digitalWrite(IMU_CHIP_SELECT, HIGH);   // Set slave select high
    short data = highData << 8 | lowData;  // Convert 8bit data into 16bit int
    return data;
}

void spi_IMU_write8(uint8_t reg, uint8_t value) {
    reg &= ~0x80;                        // Set high bit low on register to indicate write action
    digitalWrite(IMU_CHIP_SELECT, LOW);  // Set Slave select to low to begin transmission
    SPI.transfer(reg);                   // Transmit register to read from
    SPI.transfer(value);                 // Send clock pulses, to receive data
    digitalWrite(IMU_CHIP_SELECT, HIGH); // Set slave select high
}

void IMUGetData(short *data) {
    *data = spi_IMU_read16(ACCEL_XOUT_H, ACCEL_XOUT_L) + XACCEL_OFFSET;       // Form Accel X
    *(data + 1) = spi_IMU_read16(ACCEL_ZOUT_H, ACCEL_ZOUT_L) + ZACCEL_OFFSET; // Form Accel Z
    *(data + 2) = spi_IMU_read16(GYRO_YOUT_H, GYRO_YOUT_L) + YGYRO_OFFSET;    // Form Gyro Y
}

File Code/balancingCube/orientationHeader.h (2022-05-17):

#define ACCEL_CONFIG 0x14
#define ACCEL_XOUT_H 0x2D
#define ACCEL_XOUT_L 0x2E
#define ACCEL_YOUT_H 0x2F
#define ACCEL_YOUT_L 0x30
#define ACCEL_ZOUT_H 0x31
#define ACCEL_ZOUT_L 0x32
#define GYRO_CONFIG  0x01
#define GYRO_XOUT_H  0x33
#define GYRO_XOUT_L  0x34
#define GYRO_YOUT_H  0x35
#define GYRO_YOUT_L  0x36
#define GYRO_ZOUT_H  0x37
#define GYRO_ZOUT_L  0x38
#define FIFO_R_W     0x72
#define XA_OFFS_H    0x14
#define XA_OFFS_L    0x15
#define YA_OFFS_H    0x17
#define YA_OFFS_L    0x18
#define ZA_OFFS_H    0x1A
#define ZA_OFFS_L    0x1B
#define XG_OFFS_USRH 0x03
#define XG_OFFS_USRL 0x04
#define YG_OFFS_USRH 0x05
#define YG_OFFS_USRL 0x06
#define ZG_OFFS_USRH 0x07
#define ZG_OFFS_USRL 0x08

#define ACCEL_RANGE_2   0x29
#define ACCEL_RANGE_4   0x2B
#define GYRO_RANGE_250  0x11
#define GYRO_RANGE_500  0x13

#define ACCEL_SENSITIVITY_2    16384
#define ACCEL_SENSITIVITY_4    8192
#define GYRO_SENSITIVITY_250   131
#define GYRO_SENSITIVITY_500   65.5

#define PWR_MNG     0x06
#define PWR_MNG_2   0x07
#define USER_CTRL   0x03
#define USER_BANK_0 0x00
#define USER_BANK_1 0x08
#define USER_BANK_2 0x10
#define USER_BANK_3 0x18

#define XACCEL_OFFSET  0
#define YACCEL_OFFSET  0
#define ZACCEL_OFFSET  0
#define XGYRO_OFFSET   0
#define YGYRO_OFFSET   0
#define ZGYRO_OFFSET   0

#define LOW_PASS_ALPHA  0.8
#define COMP_FILT_ALPHA 0.96
